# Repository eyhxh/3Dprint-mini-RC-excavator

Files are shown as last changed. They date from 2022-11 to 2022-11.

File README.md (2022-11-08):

## 资料开源说明

机械设计图：sw2016

3D打印结构件：STL

程序代码和固件

**以上资料均在本仓库更新**

遥控器和接收板的电路原理图和pcb文件：使用立创EDA专业版设计，已在立创开源平台开源

https://oshwhub.com/eyhxh/rev6ch_2022-08-29

https://oshwhub.com/eyhxh/rc_2022-08-29

**QQ交流群：128978324**

视频演示，教程上B站视频搜索----不搞搞事不自在

或者点下面的链接

https://www.bilibili.com/video/BV1jG4y1h7KU/

## 安装说明

### 推杆3个
推杆使用N20减速电机、M3铜柱12mm长度、M3螺钉、加3D打印件组成

3个推杆仅仅推杆套和螺钉长度不同，材料，安装工艺等完全一致。

注意推杆电机要用速度快一点的电机，否则整个臂都是蜗牛速度，高速电机的力度经测试完全足够！

挖斗推杆：螺钉长度35mm  推杆套长度40mm

小臂推杆：螺钉长度50mm  推杆套长度55mm

大臂推杆：螺钉长度45mm  推杆套长度50mm

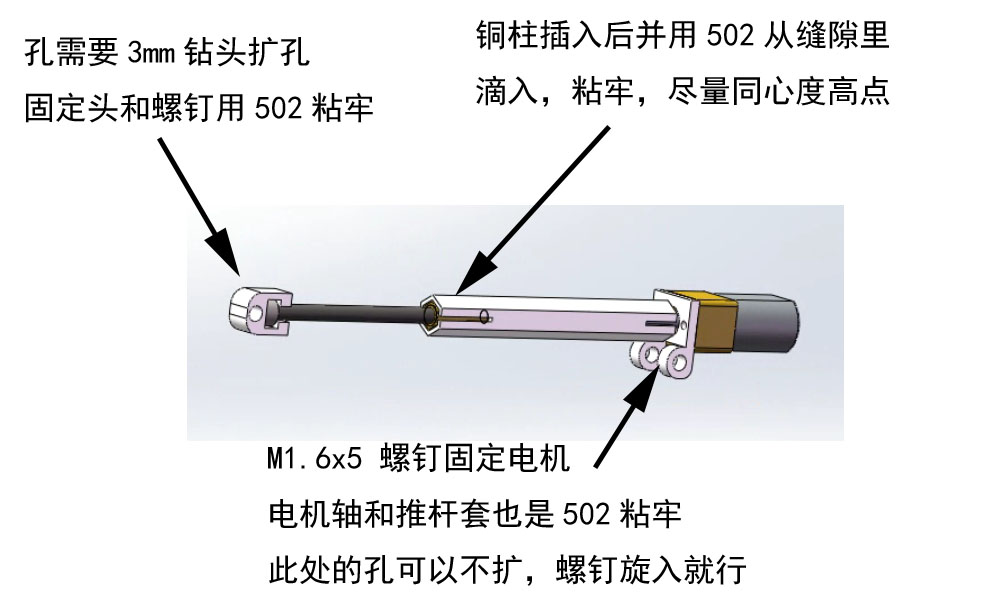
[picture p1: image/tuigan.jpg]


### 主体结构
主体结构比较简单，如图安装即可
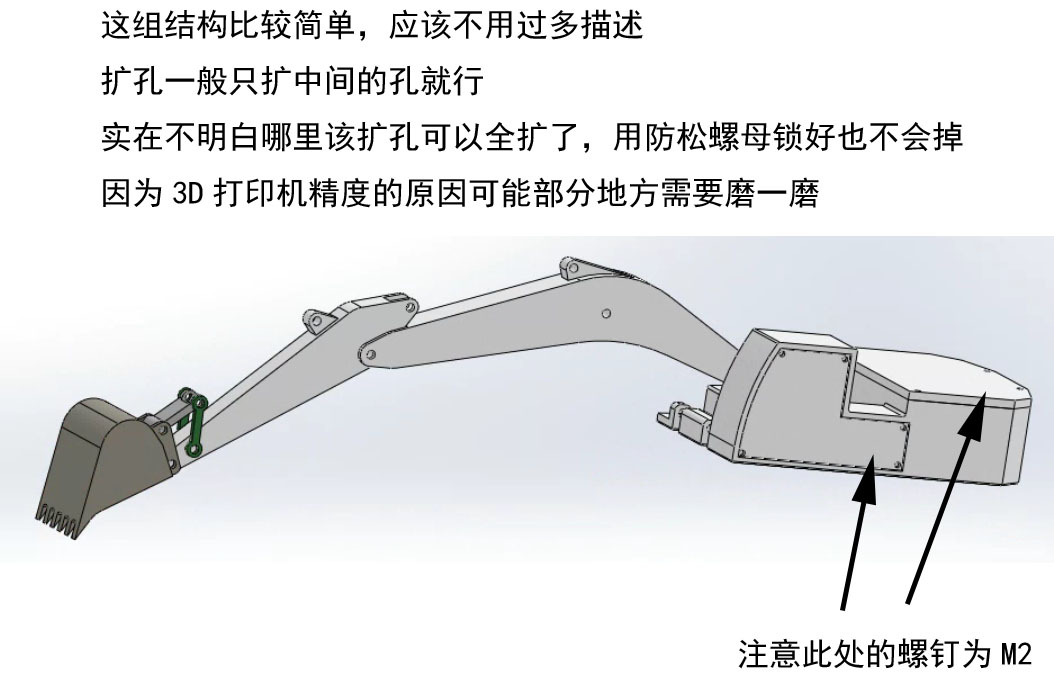
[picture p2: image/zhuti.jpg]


### 底盘旋转电机
底盘旋转电机需要先安装好，注意使用低速电机，否则底盘和电风扇一样快
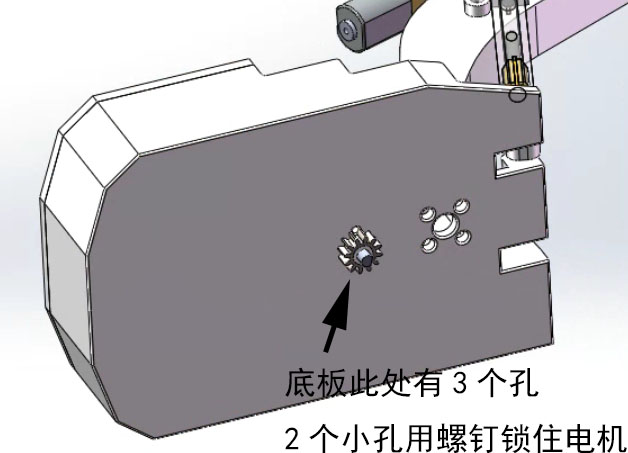
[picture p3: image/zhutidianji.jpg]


### 底盘旋转结构 
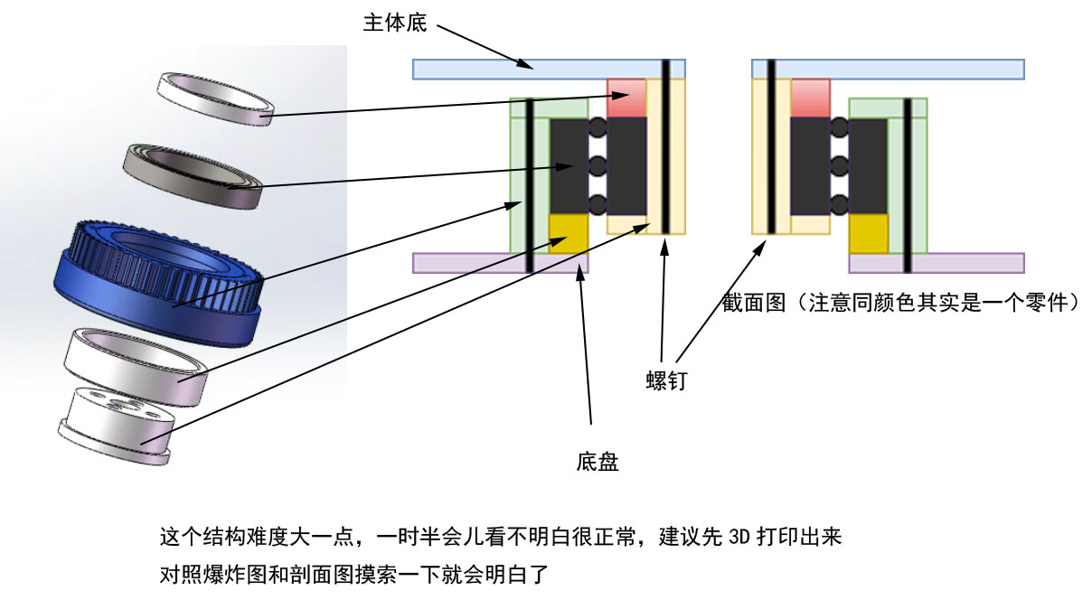
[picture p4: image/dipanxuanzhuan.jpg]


### 底盘结构
底盘2个电机建议使用低速电机，否则挖掘机和AE86一样
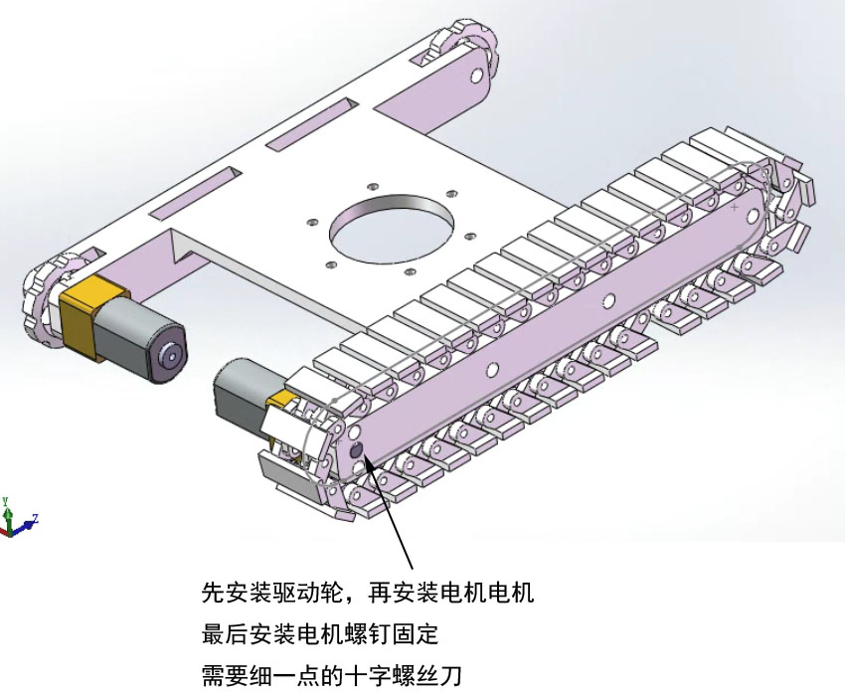
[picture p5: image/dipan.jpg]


### 履带效果
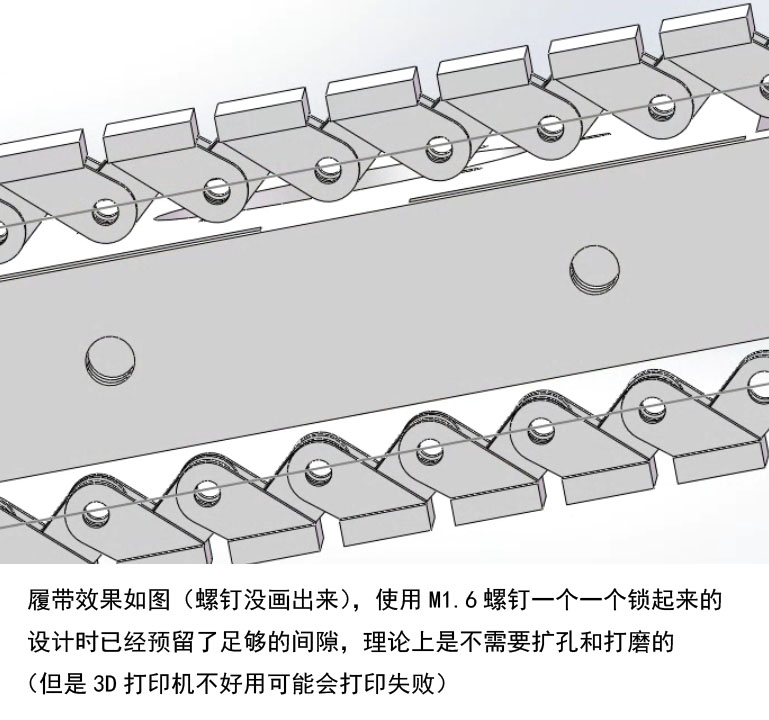
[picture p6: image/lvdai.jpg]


## 更新日志
2022年11月8日16:29:45

1、添加初版代码、资料

2、如有问题可以在QQ群反馈

3、目前版本存在一些已知问题，但是整体上完成度已经较高，当然后续会不断改进。多谢关注

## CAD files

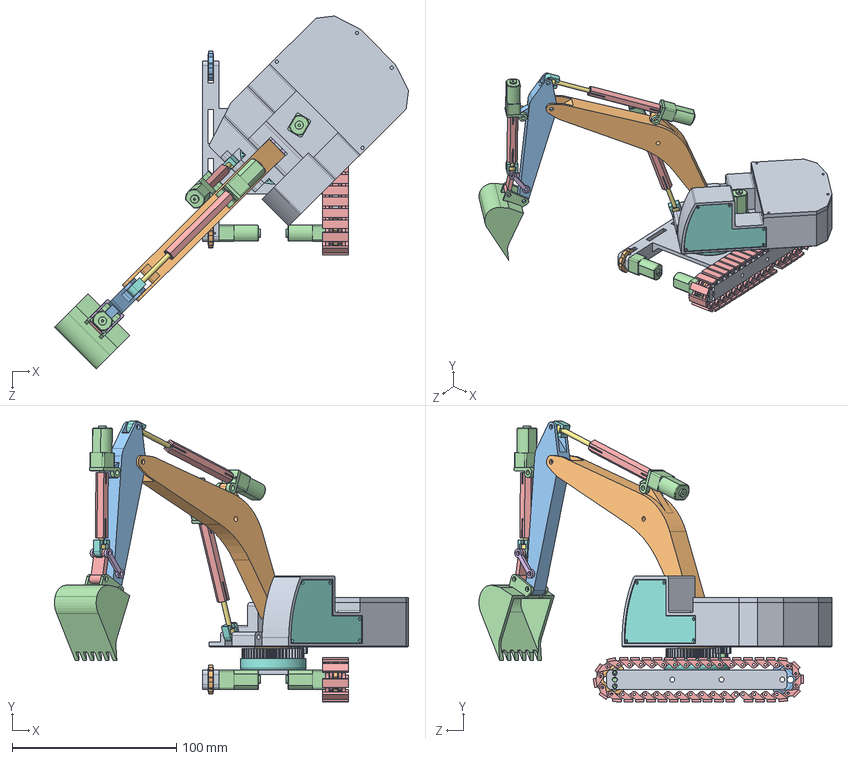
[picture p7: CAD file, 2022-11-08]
机械部分/工程文件/试装1.SLDASM
215.7 x 171.1 x 215.0 mm
底盘
驱动轮2 x 2
从动轮3 x 2
N20减速电机 x 6
履带模块4 x 37
轴承内套
轴承20-32-7
轴承外套
spur gear_gb x 2
轴承内套垫高
N20电机固定 x 3
推杆套 x 3
M3铜柱 x 3
M3螺钉 x 3
螺钉固定头 x 3
主体底
大臂
小臂
挖斗
挖斗连杆1
挖斗连杆2 x 2
pcb
电池仓盖
齿轮内孔^主轴齿轮适配体

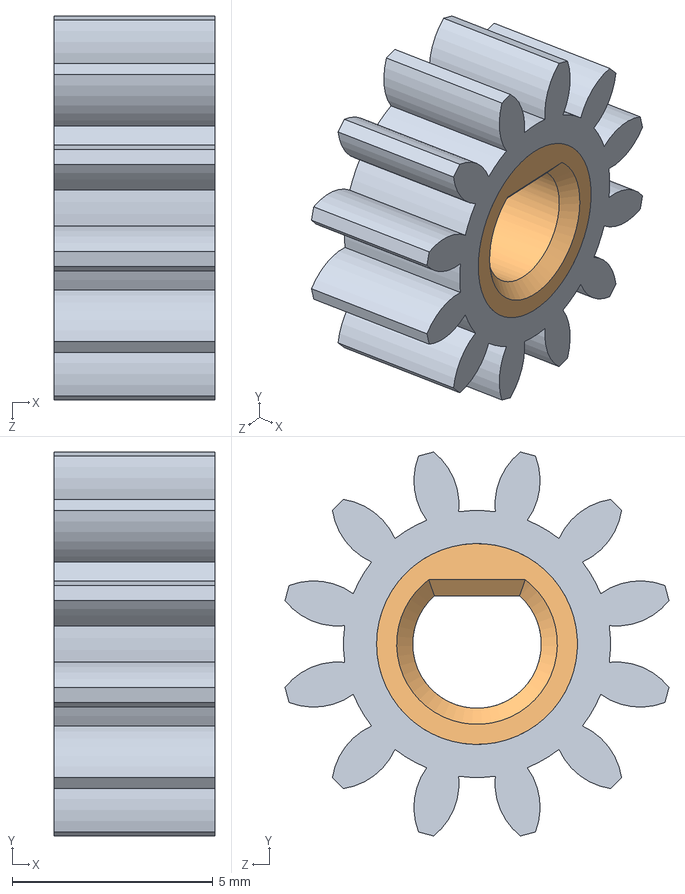
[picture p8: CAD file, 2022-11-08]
机械部分/工程文件/主轴齿轮适配体.SLDASM
4.00 x 9.56 x 9.56 mm
spur gear_gb
齿轮内孔^主轴齿轮适配体

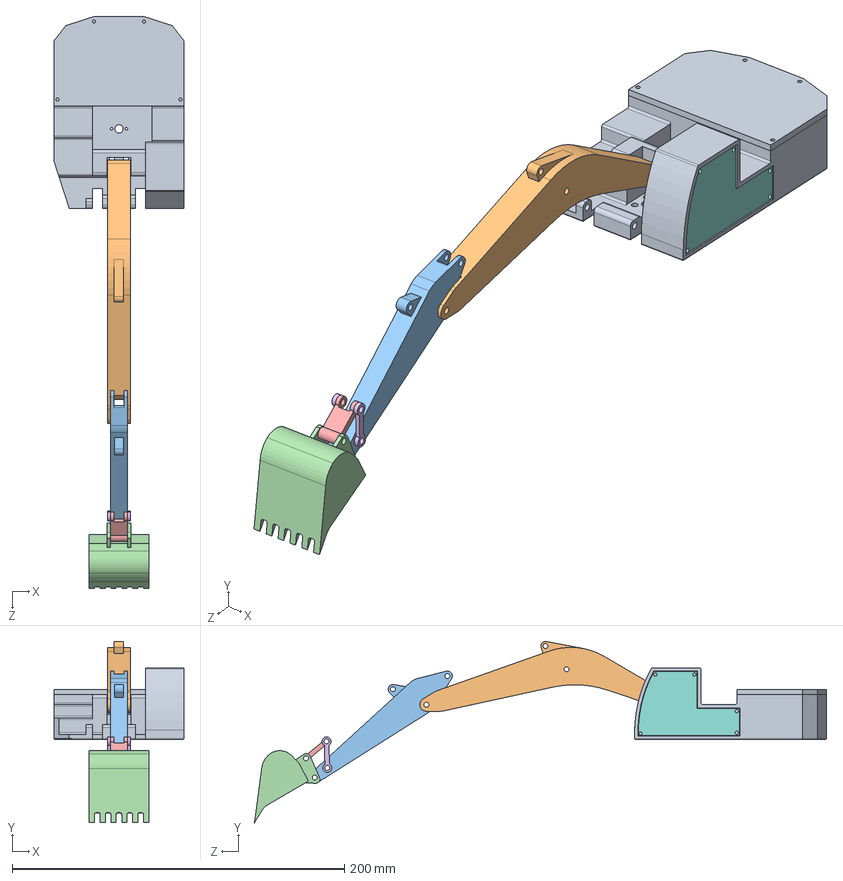
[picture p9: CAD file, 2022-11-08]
机械部分/工程文件/主体系统.sldasm
78.0 x 109.0 x 344.2 mm
主体底
大臂
小臂
挖斗
挖斗连杆1
挖斗连杆2 x 2
pcb
控制板壳
电池仓盖

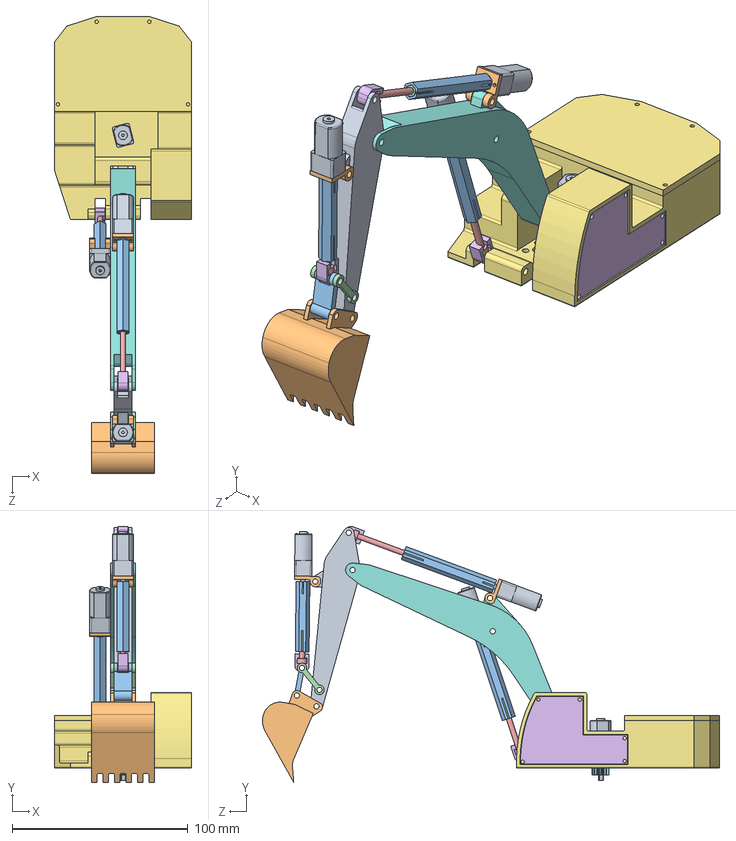
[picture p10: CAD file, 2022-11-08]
机械部分/工程文件/主体带推杆系统.sldasm
78.0 x 145.8 x 260.0 mm
N20减速电机 x 4
N20电机固定 x 3
推杆套 x 3
M3铜柱 x 3
M3螺钉 x 3
螺钉固定头 x 3
主体底
大臂
小臂
挖斗
挖斗连杆1
挖斗连杆2 x 2
pcb
电池仓盖
spur gear_gb
齿轮内孔^主轴齿轮适配体

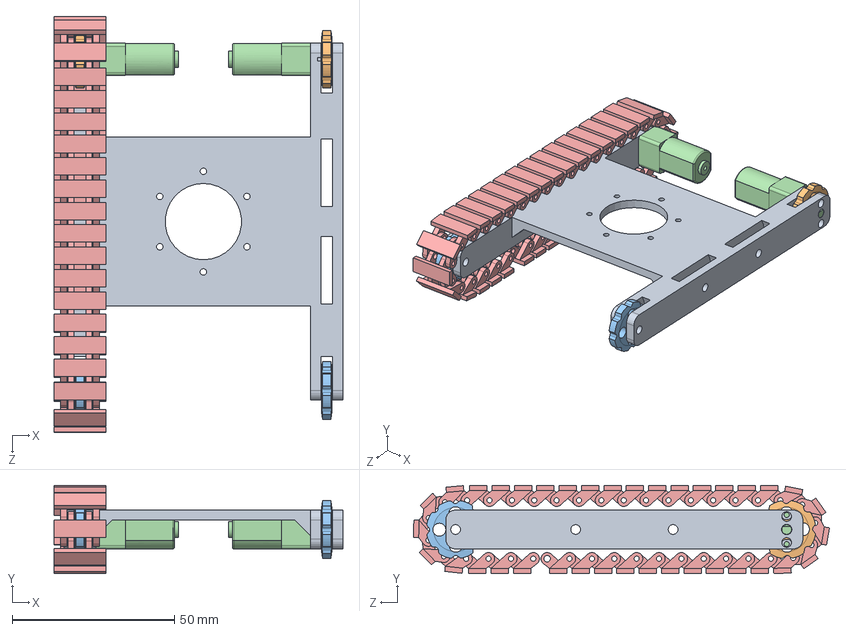
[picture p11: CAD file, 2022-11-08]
机械部分/工程文件/底盘系统.SLDASM
89.0 x 27.2 x 128.1 mm
底盘
驱动轮2 x 2
从动轮3 x 2
N20减速电机 x 2
履带模块4 x 37

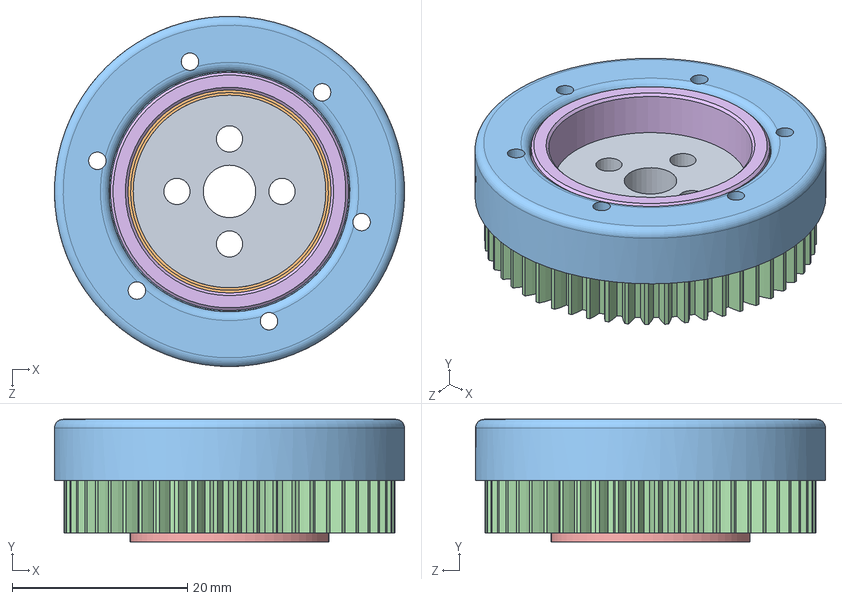
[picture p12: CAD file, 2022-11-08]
机械部分/工程文件/新轴承系统.SLDASM
40.0 x 14.0 x 40.0 mm
轴承内套
轴承20-32-7
轴承外套
spur gear_gb
轴承内套垫高

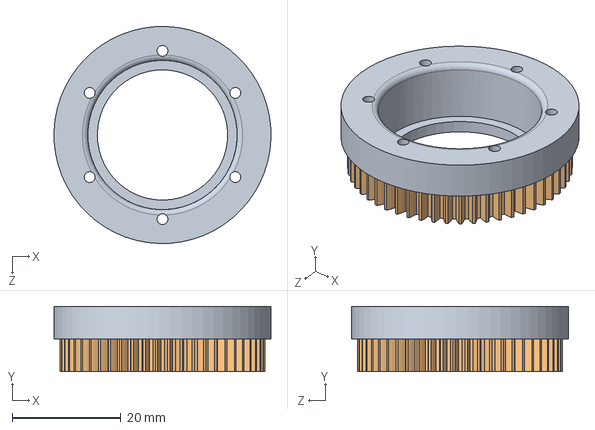
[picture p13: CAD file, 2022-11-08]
机械部分/工程文件/轴承外套带齿轮.sldasm
40.0 x 12.0 x 40.0 mm
轴承外套
spur gear_gb

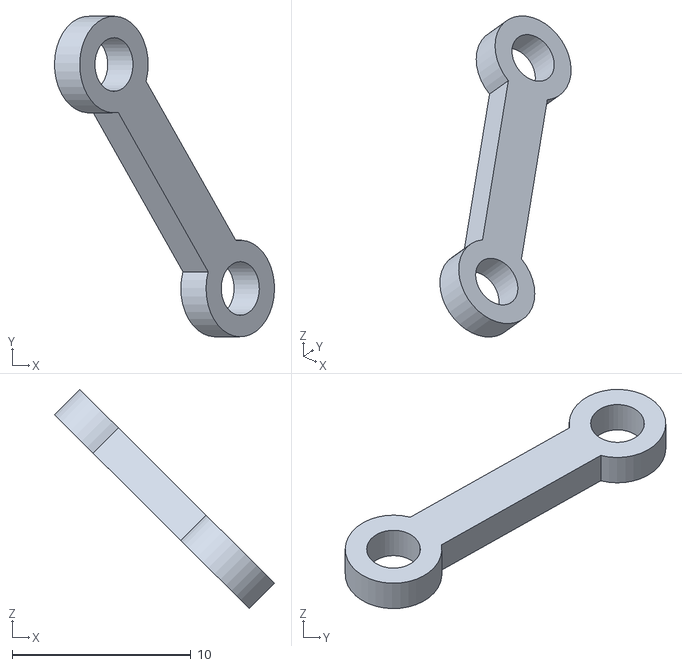
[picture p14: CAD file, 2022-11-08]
机械部分/3D打印机STL文件/主体部分/试装1 - 主体带推杆系统-1 主体系统-1 挖斗连杆2-1.STL
12.3 x 17.9 x 12.3

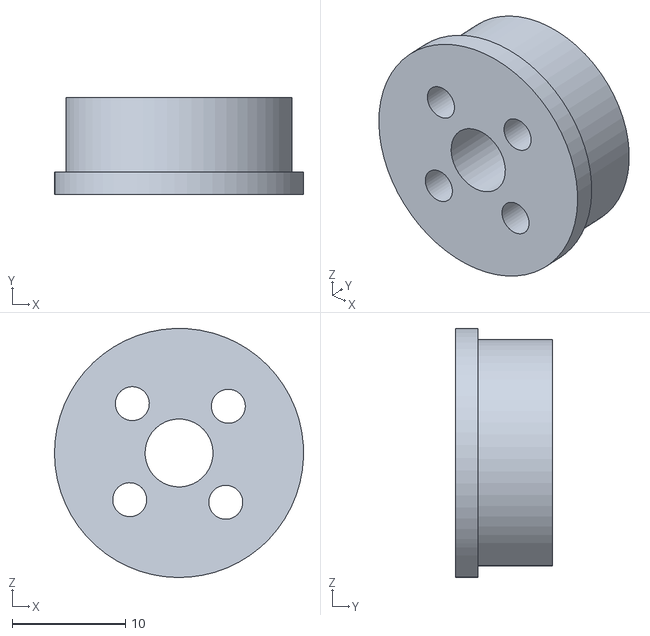
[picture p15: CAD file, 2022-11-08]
机械部分/3D打印机STL文件/底盘旋转结构/试装1 - 新轴承系统-1 轴承内套-1.STL
22.0 x 8.60 x 22.0

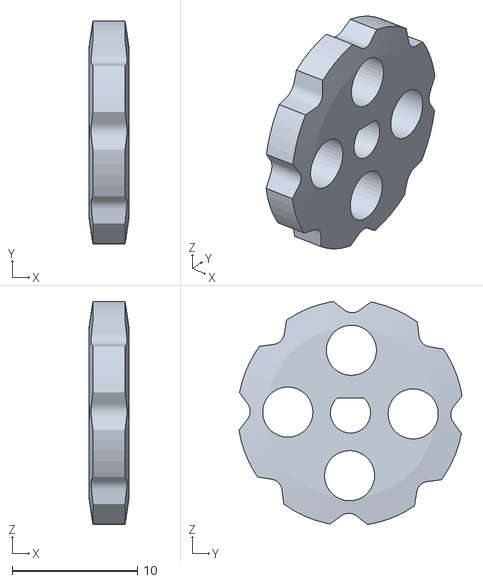
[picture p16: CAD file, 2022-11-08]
机械部分/3D打印机STL文件/底盘部分/试装1 - 底盘系统-1 驱动轮2-4.STL
3.20 x 17.8 x 17.8

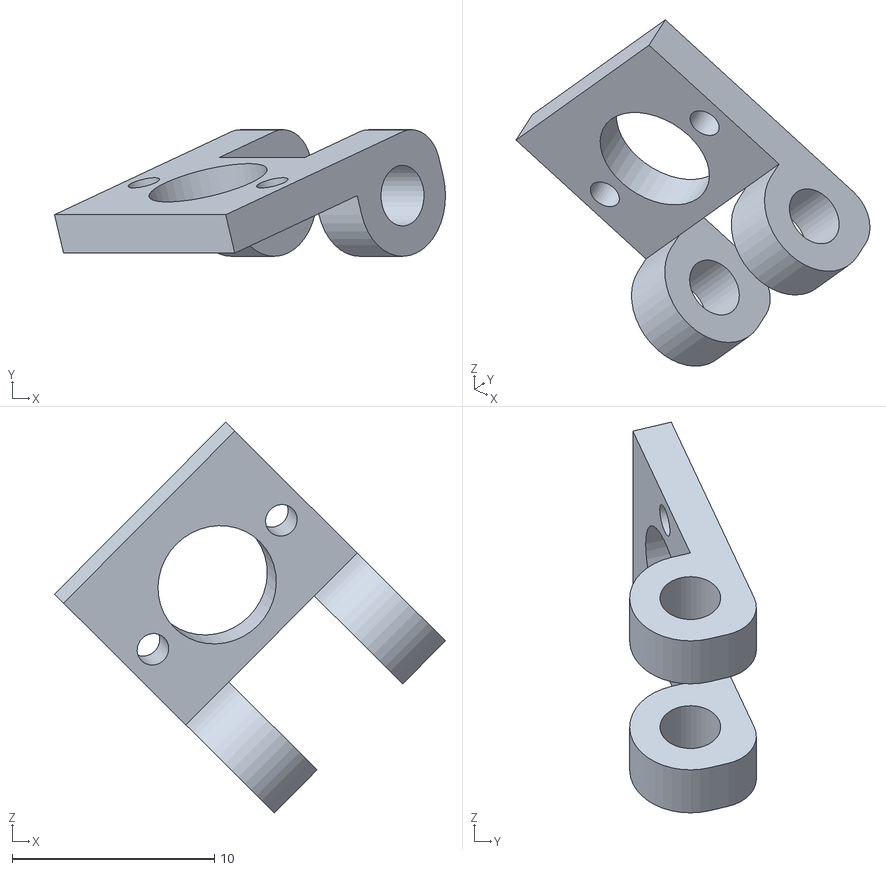
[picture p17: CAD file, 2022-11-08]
机械部分/3D打印机STL文件/推杆部分/试装1 - 主体带推杆系统-1 推杆1-2 N20电机固定-1.STL
19.3 x 6.26 x 19.3

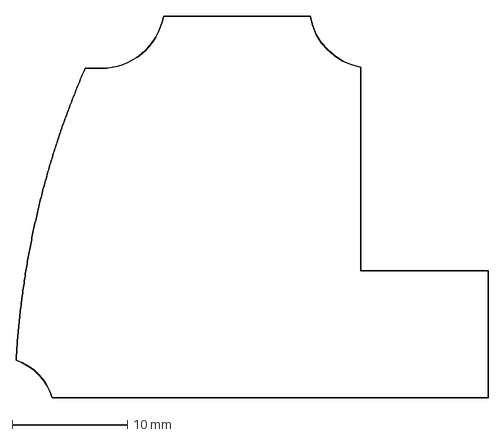
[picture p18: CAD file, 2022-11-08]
机械部分/工程文件/pcb^主体系统.DXF
40.9 x 33.0 mm

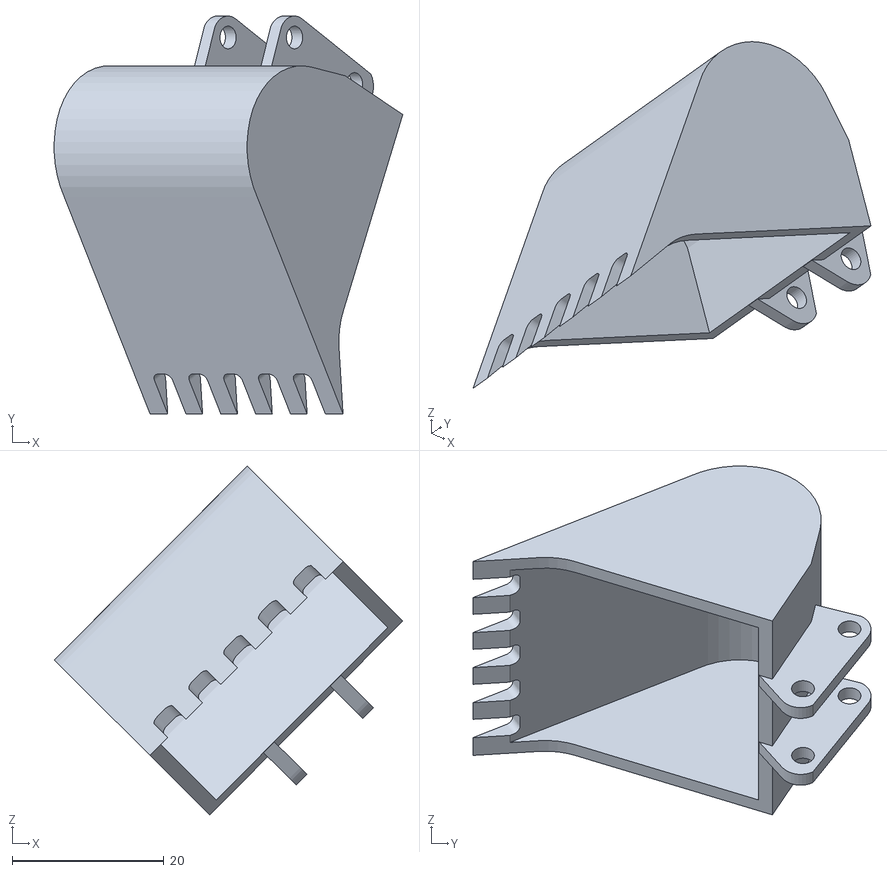
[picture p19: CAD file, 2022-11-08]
机械部分/3D打印机STL文件/主体部分/试装1 - 主体带推杆系统-1 主体系统-1 挖斗-1.STL
45.9 x 52.4 x 45.9

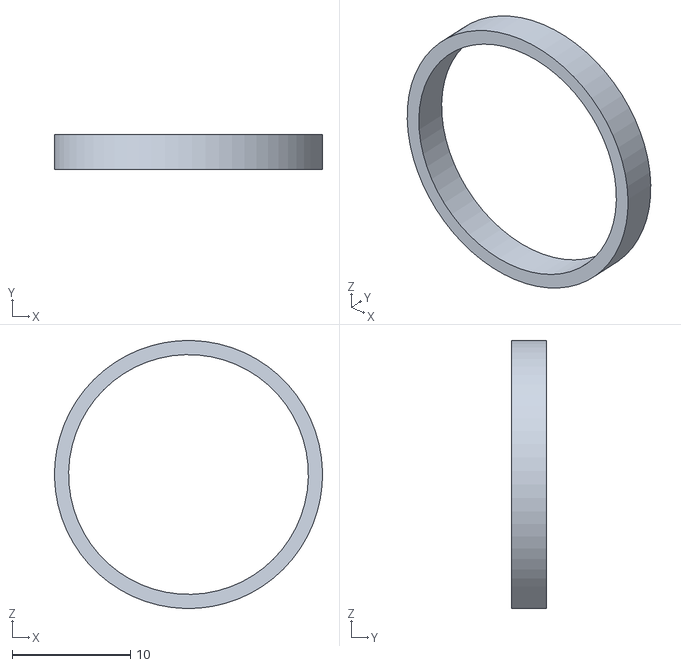
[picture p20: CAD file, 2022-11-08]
机械部分/3D打印机STL文件/底盘旋转结构/试装1 - 新轴承系统-1 轴承内套垫高-1.STL
22.7 x 3.00 x 22.7

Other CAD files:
机械部分/工程文件/推杆1.SLDASM
机械部分/3D打印机STL文件/底盘部分/试装1 - 底盘系统-1 从动轮3-9.STL
机械部分/3D打印机STL文件/推杆部分/试装1 - 主体带推杆系统-1 推杆1-3 螺钉固定头-1.STL
机械部分/工程文件/履带模块2.SLDPRT
机械部分/3D打印机STL文件/主体部分/试装1 - 主体带推杆系统-1 主体系统-1 主体底-1.STL
机械部分/3D打印机STL文件/主体部分/试装1 - 主体带推杆系统-1 主体系统-1 大臂-1.STL
机械部分/3D打印机STL文件/主体部分/试装1 - 主体带推杆系统-1 主体系统-1 小臂-1.STL
机械部分/3D打印机STL文件/主体部分/试装1 - 主体带推杆系统-1 主体系统-1 挖斗连杆1-1.STL
机械部分/3D打印机STL文件/主体部分/试装1 - 主体带推杆系统-1 主体系统-1 挖斗连杆2-2.STL
机械部分/3D打印机STL文件/底盘旋转结构/主轴齿轮适配体.STL
机械部分/3D打印机STL文件/底盘旋转结构/轴承外套垫高.STL
机械部分/3D打印机STL文件/底盘旋转结构/轴承外套带齿轮.STL
机械部分/3D打印机STL文件/底盘部分/试装1 - 底盘系统-1 从动轮3-4.STL
机械部分/3D打印机STL文件/底盘部分/试装1 - 底盘系统-1 履带模块4-223.STL
机械部分/3D打印机STL文件/底盘部分/试装1 - 底盘系统-1 底盘-1.STL
机械部分/3D打印机STL文件/底盘部分/试装1 - 底盘系统-1 驱动轮2-3.STL
机械部分/3D打印机STL文件/推杆部分/试装1 - 主体带推杆系统-1 推杆1-1 N20电机固定-1.STL
机械部分/3D打印机STL文件/推杆部分/试装1 - 主体带推杆系统-1 推杆1-1 推杆套-1.STL
机械部分/3D打印机STL文件/推杆部分/试装1 - 主体带推杆系统-1 推杆1-1 螺钉固定头-1.STL
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

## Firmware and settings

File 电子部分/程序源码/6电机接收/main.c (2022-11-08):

#include "system.h"
#include "nrf24l01.h"
#include "string.h"
#include "stdio.h"

#define LED_G P27
#define LED_R P26

#define LED_ON 0
#define LED_OFF 1

void delay()
{
    int i, j;

    for (i = 0; i < 1000; i++)
        for (j = 0; j < 500; j++)
            ;
}

void motor_test()
{
    P25 = 0;
    P24 = 1;

    P23 = 0;
    P22 = 1;

    P21 = 0;
    P20 = 1;

    P37 = 0;
    P36 = 1;

    P35 = 0;
    P34 = 1;

    P33 = 0;
    P32 = 1;
    sendString("motor foreward\r\n");
    delay();
    P25 = 1;
    P24 = 0;

    P23 = 1;
    P22 = 0;

    P21 = 1;
    P20 = 0;

    P37 = 1;
    P36 = 0;

    P35 = 1;
    P34 = 0;

    P33 = 1;
    P32 = 0;
    sendString("motor backward\r\n");
    delay();
}

void motor0(u8 pwm)
{
    if (pwm > 177)
    {
        P25 = 1;
        P24 = 0;
    }
    else if (pwm < 77)
    {
        P25 = 0;
        P24 = 1;
    }
    else
    {
        P25 = 0;
        P24 = 0;
    }
}
void motor1(u8 pwm)
{
    if (pwm > 177)
    {
        P23 = 1;
        P22 = 0;
    }
    else if (pwm < 77)
    {
        P23 = 0;
        P22 = 1;
    }
    else
    {
        P23 = 0;
        P22 = 0;
    }
}
void motor2(u8 pwm)
{
    if (pwm > 177)
    {
        P21 = 1;
        P20 = 0;
    }
    else if (pwm < 77)
    {
        P21 = 0;
        P20 = 1;
    }
    else
    {
        P21 = 0;
        P20 = 0;
    }
}
void motor3(u8 pwm)
{
    if (pwm > 177)
    {
        P37 = 1;
        P36 = 0;
    }
    else if (pwm < 77)
    {
        P37 = 0;
        P36 = 1;
    }
    else
    {
        P37 = 0;
        P36 = 0;
    }
}
void motor4(u8 pwm)
{
    if (pwm > 177)
    {
        P35 = 1;
        P34 = 0;
    }
    else if (pwm < 77)
    {
        P35 = 0;
        P34 = 1;
    }
    else
    {
        P35 = 0;
        P34 = 0;
    }
}
void motor5(u8 pwm)
{
    if (pwm > 177)
    {
        P33 = 1;
        P32 = 0;
    }
    else if (pwm < 77)
    {
        P33 = 0;
        P32 = 1;
    }
    else
    {
        P33 = 0;
        P32 = 0;
    }
}

#if 0
void motorCtrl(u8 idx, u8 value)
{
    if (idx == 0)
    {
        motor0(value);
    }
    else if (idx == 1)
    {
        motor1(value);
    }
    else if (idx == 2)
    {
        motor2(value);
    }
    else if (idx == 3)
    {
        motor3(value);
    }
    else if (idx == 4)
    {
        motor4(value);
    }
    else if (idx == 5)
    {
        motor5(value);
    }
}
#else

#define MAIN_Fosc 11059200UL //定义主时钟
#define Timer0_Rate 25000    //中断频率

#define Timer0_Reload (65536UL - (MAIN_Fosc / Timer0_Rate)) // Timer 0 重装值

//************** PWM8 变量和常量以及IO口定义 ***************
//********************  8通道8 bit 软PWM    ********************

#define PWM_DUTY_MAX 10 // 0~255    PWM周期, 最大255
#define PWM_ON 1        // 定义占空比的电平, 1 或 0

#define PWM_OFF (!PWM_ON)
#define PWM_ALL_ON (0xff * PWM_ON)

u8 pwm_duty; //周期计数值
u8 pwm[16];  // pwm0~pwm15 为0至15路PWM的宽度值

u8 bdata PWM_temp1, PWM_temp2; //影射一个RAM，可位寻址，输出时同步刷新
sbit P_PWM0 = PWM_temp1 ^ 0;   //  定义影射RAM每位对应的IO
sbit P_PWM1 = PWM_temp1 ^ 1;
sbit P_PWM2 = PWM_temp1 ^ 2;
sbit P_PWM3 = PWM_temp1 ^ 3;
sbit P_PWM4 = PWM_temp1 ^ 4;
sbit P_PWM5 = PWM_temp1 ^ 5;
sbit P_PWM6 = PWM_temp1 ^ 6;
sbit P_PWM7 = PWM_temp1 ^ 7;
sbit P_PWM8 = PWM_temp2 ^ 0;
sbit P_PWM9 = PWM_temp2 ^ 1;
sbit P_PWM10 = PWM_temp2 ^ 2;
sbit P_PWM11 = PWM_temp2 ^ 3;
sbit P_PWM12 = PWM_temp2 ^ 4;
sbit P_PWM13 = PWM_temp2 ^ 5;
sbit P_PWM14 = PWM_temp2 ^ 6;
sbit P_PWM15 = PWM_temp2 ^ 7;

//定义所有io口
#if 0
sbit pwmio0 = P3 ^ 2;
sbit pwmio1 = P3 ^ 3;
sbit pwmio2 = P3 ^ 4;
sbit pwmio3 = P3 ^ 5;
sbit pwmio4 = P3 ^ 6;
sbit pwmio5 = P3 ^ 7;
sbit pwmio6 = P2 ^ 0;
sbit pwmio7 = P2 ^ 1;
sbit pwmio8 = P2 ^ 2;
sbit pwmio9 = P2 ^ 3;
sbit pwmio10 = P2 ^ 4;
sbit pwmio11 = P2 ^ 5;
#endif
sbit pwmio0 = P2 ^ 2;
sbit pwmio1 = P2 ^ 3;

sbit pwmio2 = P3 ^ 6;
sbit pwmio3 = P3 ^ 7;

sbit pwmio4 = P2 ^ 0;
sbit pwmio5 = P2 ^ 1;

sbit pwmio6 = P2 ^ 4;
sbit pwmio7 = P2 ^ 5;

sbit pwmio8 = P3 ^ 4;
sbit pwmio9 = P3 ^ 5;

sbit pwmio10 = P3 ^ 2;
sbit pwmio11 = P3 ^ 3;

void softPWMInit()
{
    AUXR |= (1 << 7);          // Timer0 set as 1T mode
    TMOD &= ~(1 << 2);         // Timer0 set as Timer
    TMOD &= ~0x03;             // Timer0 set as 16 bits Auto Reload
    TH0 = Timer0_Reload / 256; // Timer0 Load
    TL0 = Timer0_Reload % 256;
    ET0 = 1; // Timer0 Interrupt Enable
    PT0 = 1; //高优先级
    TR0 = 1; // Timer0 Run
    EA = 1;  //打开总中断
}

/********************** Timer0 1ms中断函数 ************************/
void timer0(void) interrupt 1
{
    // P1 = PWM_temp1;         //影射RAM输出到实际的PWM端口
    // P2 = PWM_temp2;
    pwmio0 = P_PWM0;
    pwmio1 = P_PWM1;
    pwmio2 = P_PWM2;
    pwmio3 = P_PWM3;
    pwmio4 = P_PWM4;
    pwmio5 = P_PWM5;
    pwmio6 = P_PWM6;
    pwmio7 = P_PWM7;
    pwmio8 = P_PWM8;
    pwmio9 = P_PWM9;
    pwmio10 = P_PWM10;
    pwmio11 = P_PWM11;
    if (++pwm_duty == PWM_DUTY_MAX) // PWM周期结束，重新开始新的周期
    {
        pwm_duty = 0;
        PWM_temp1 = PWM_ALL_ON;
        PWM_temp2 = PWM_ALL_ON;
    }
    ACC = pwm_duty;
    if (ACC == pwm[0])
        P_PWM0 = PWM_OFF; //判断PWM占空比是否结束
    if (ACC == pwm[1])
        P_PWM1 = PWM_OFF;
    if (ACC == pwm[2])
        P_PWM2 = PWM_OFF;
    if (ACC == pwm[3])
        P_PWM3 = PWM_OFF;
    if (ACC == pwm[4])
        P_PWM4 = PWM_OFF;
    if (ACC == pwm[5])
        P_PWM5 = PWM_OFF;
    if (ACC == pwm[6])
        P_PWM6 = PWM_OFF;
    if (ACC == pwm[7])
        P_PWM7 = PWM_OFF;
    if (ACC == pwm[8])
        P_PWM8 = PWM_OFF;
    if (ACC == pwm[9])
        P_PWM9 = PWM_OFF;
    if (ACC == pwm[10])
        P_PWM10 = PWM_OFF;
    if (ACC == pwm[11])
        P_PWM11 = PWM_OFF;
}

// for test idx 0~5  pwmvalue 0-128
void setPWM(u8 idx, u8 pwmValue)
{
    if(pwmValue <= 20) //避开摇杆的中间位置
        pwmValue = 0;
    else
        pwmValue -= 20;

    pwmValue /= 10; 

    if(pwmValue > 10) // 物理pwm范围 0-10
        pwmValue = 10;

    if (idx < 12)
    {
        pwm[idx] = pwmValue;
    }
}


/*
    0~255 input
*/
void motorCtrl(u8 index, u8 pwmvalue, u8 reverse)
{
    int pwmin = pwmvalue;

    int val;
    if (reverse)
        val = 128 - pwmin;
    else
        val = pwmin - 128;

//val范围 -128 ~ 127
    if (val > 0)
    {
        setPWM(index * 2, val);
        setPWM(index * 2 + 1, 0);
    }
    else if (val < 0)
    {
        setPWM(index * 2, 0);
        setPWM(index * 2 + 1, -val);
    }
    else
    {
        setPWM(index * 2, 0);
        setPWM(index * 2 + 1, 0);
    }
}

#endif

idata u8 nrf_rx_buf[32];
#if 0
xdata u8 buf[64] = {0};
void adcSendUart()
{
    memset(buf, 0, 64);
    sprintf(buf, "%bx %bx %bx %bx %bx %bx %bx %bx\r\n",
            adcvalue[0], adcvalue[1], adcvalue[2], adcvalue[3], adcvalue[4], adcvalue[5], adcvalue[6], adcvalue[7]);

    sendString(buf);
}
#endif
void main()
{
    delay_ms(100); // 延时待系统稳定
    softPWMInit();

    //引脚复用初始化
    P1M0 = (1 << 2) + (1 << 3) + (1 << 4) + (1 << 5); // CE CSN SCK MOSI 设为PP输出 MISO IRQ默认
    P1M1 = 0x0;

    P2M0 = (1 << 0) + (1 << 1) + (1 << 2) + (1 << 3) + (1 << 4) + (1 << 5); //电机输出设为pp输出
    P2M1 = 0x0;

    P3M0 = (1 << 2) + (1 << 3) + (1 << 4) + (1 << 5) + (1 << 6) + (1 << 7);
    P3M1 = 0x0;
    // NRF_CE = 1;

    serial_open(); // 打开串口
    sendString("hello init\r\n");
    // 等待检测到NRF24L01，程序才会向下执行
    while (NRF24L01_Check())
    {
        LED_R = LED_ON;
        sendString("check nrf...\r\n");
        delay();
    }
    LED_R = LED_OFF;
    sendString("check nrf ok!\r\n");
    NRF24L01_RX_Mode(); // 配置NRF24L01为接收模式

    while (1)
    {
#if 0
        NRF_CE = 0;
        NRF24L01_RW_Reg(WRITE_REG + CONFIG, 0x0f); // IRQ收发完成中断响应，16位CRC	，主接收
				NRF_CE = 1;
#endif

        if (NRF24L01_RxPacket(nrf_rx_buf)) // || !NRF_IRQ)
        {
            // STA_LED=~STA_LED; // 翻转指示灯
            // for(i=0;i<32;i++)
            // senddata(rece_buf[i]);
            // sendString("rev data\r\n");
            /*
                电机排序  0挖斗   1小臂   2大臂  3旋转  4左 5右
                遥控信号排序  0左y 1左x  2右y 3右x  4副1y   5副2y


            */
            motorCtrl(0, nrf_rx_buf[0], 1);
            motorCtrl(1, nrf_rx_buf[1], 0);
            motorCtrl(2, nrf_rx_buf[2], 1);
            motorCtrl(3, nrf_rx_buf[3], 1);
            motorCtrl(4, nrf_rx_buf[4], 0);
            motorCtrl(5, nrf_rx_buf[5], 0);

            LED_G = LED_ON;
            delay_ms(2);
            LED_G = LED_OFF;
        }
        else
        {
            delay_ms(10);
        }
    }
}

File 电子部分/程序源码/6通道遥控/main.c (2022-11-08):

#include "system.h"
#include "nrf24l01.h"
#include "string.h"
#include "stdio.h"



#define LED_G P26
#define LED_R P27

#define LED_ON 0
#define LED_OFF 1

void delay()
{
    int i, j;

    for (i = 0; i < 1000; i++)
        for (j = 0; j < 500; j++)
            ;
}

/*----------------------------
ADC相关数据结构
----------------------------*/
#define ADC_POWER 0x80   // ADC电源控制位
#define ADC_FLAG 0x10    // ADC完成标志
#define ADC_START 0x08   // ADC起始控制位
#define ADC_SPEEDLL 0x00 // 540个时钟
#define ADC_SPEEDL 0x20  // 360个时钟
#define ADC_SPEEDH 0x40  // 180个时钟
#define ADC_SPEEDHH 0x60 // 90个时钟

u8 ch = 0; // ADC通道号
u8 adcvalue[8] = {0};

/*----------------------------
ADC中断服务程序
----------------------------*/
void adc_isr() interrupt 5
{
    ADC_CONTR &= !ADC_FLAG; //清除ADC中断标志

    // SendData(ch);                   //显示通道号
    // SendData(ADC_RES);              //读取高8位结果并发送到串口
    adcvalue[ch] = ADC_RES;
    //    SendData(ADC_LOW2);           //显示低2位结果

    if (++ch > 7)
        ch = 0; //切换到下一个通道
    ADC_CONTR = ADC_POWER | ADC_SPEEDLL | ADC_START | ch;
}

/*----------------------------
初始化ADC
----------------------------*/
void InitADC()
{
#if 0
    // io复用设置
    P0M0 = 0x00;
    P0M1 = 0x00;
    P1M0 = 0x00;
    P1M1 = 0x00;
    P2M0 = 0x00;
    P2M1 = 0x00;
    P3M0 = 0x00;
    P3M1 = 0x00;
    P4M0 = 0x00;
    P4M1 = 0x00;
    P5M0 = 0x00;
    P5M1 = 0x00;
    P6M0 = 0x00;
    P6M1 = 0x00;
    P7M0 = 0x00;
    P7M1 = 0x00;
#endif

    P1ASF = 0xff; //设置P1口为AD口
    ADC_RES = 0;  //清除结果寄存器
    ADC_CONTR = ADC_POWER | ADC_SPEEDLL | ADC_START | ch;
    delay_ms(10); // ADC上电并延时
    IE = 0xa0;    //使能ADC中断
}

#if 1
xdata u8 buf[32] = {0};
void adcSendUart()
{
    memset(buf, 0, 64);
    sprintf(buf, "%bx %bx %bx %bx %bx %bx %bx %bx\r\n",
            adcvalue[0], adcvalue[1], adcvalue[2], adcvalue[3], adcvalue[4], adcvalue[5], adcvalue[6], adcvalue[7]);

    sendString(buf);
}
#endif
idata u8 TxBuf[8] = {0x00};
u8 ret;
void main()
{
    delay_ms(100); // 延时待系统稳定

    P2M0 = 0x20; // NRF CE 设为推挽
    P2M1 = 0x0;

    LED_G = LED_OFF;
    LED_R = LED_OFF;
    serial_open(); // 打开串口
    sendString("hello init\r\n");

    InitADC(); //初始化ADC

#if 1
    // 等待检测到NRF24L01，程序才会向下执行
    while (NRF24L01_Check())
    {
        LED_R = LED_ON;
        sendString("check nrf...\r\n");
        delay();
    }
    LED_R = LED_OFF;
    sendString("check nrf ok!\r\n");
    NRF24L01_TX_Mode(); // 配置NRF24L01为接收模式
#endif
    while (1)
    {
#if 0
        LED_G = 0;
        LED_R = 0;
        delay_ms(50);
        LED_G = 1;
        LED_R = 1;
        delay_ms(50);
#else        
        //adcSendUart();

        TxBuf[0] = adcvalue[3]; //左y 左x  右y 右x 副1y 副2y
        TxBuf[1] = adcvalue[1];
        TxBuf[2] = adcvalue[6];
        TxBuf[3] = adcvalue[2];
        TxBuf[4] = adcvalue[4];
        TxBuf[5] = adcvalue[5];

        sendString("send nrf\r\n");
        ret = NRF24L01_TxPacket(TxBuf);
        if (ret & TX_OK)
        {
            LED_G = LED_ON;
            delay_ms(10);
            LED_G = LED_OFF;
            sendString("send nrf done\r\n");
        }
        if (ret & IRQ_TIMEOUT)
        {
            LED_R = LED_ON;
            delay_ms(10);
            LED_R = LED_OFF;
            sendString("send nrf irq timeout error\r\n");
        }
        if (ret & MAX_TX)
        {
            LED_R = LED_ON;
            delay_ms(10);
            LED_R = LED_OFF;
            sendString("send nrf max tx error\r\n");
        }

        delay_ms(50);
#endif
    }
}

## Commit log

2022-11-08 添加初始代码
    [M3螺钉.SLDPRT, M3铜柱.SLDPRT, N20减速电机.SLDPRT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]
2022-11-08 更新安装指导图片说明
